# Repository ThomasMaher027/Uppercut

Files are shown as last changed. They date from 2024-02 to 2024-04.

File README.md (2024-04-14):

# Projet S4GRO 2024 - Uppercut
Le Uppercut est un projet ayant pour but de concevoir un bras robotique de type *Shadow boxer*, inspiré du film [*Real Steel*](https://youtu.be/wD0goULgueE?si=wrtzg6bM562aRAEw).
Le projet s'est divisé en 3 objectifs : concevoir un bras robotique à 4 axes, atteindre des positions cibles avec précision et utiliser une caméra pour contrôler le robot. 

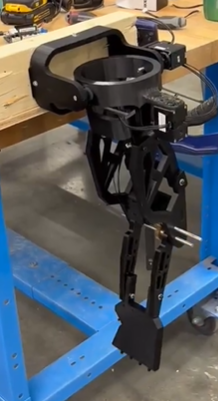
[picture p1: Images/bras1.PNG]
image du bras robotique


##  Guide du répertoire
Voici un guide de l'organisation des dossiers :
- Le dossier [*Arduino*](https://github.com/ThomasMaher027/Uppercut/tree/main/Arduino) contient le code utilisé sur la carte Arduino pour contrôler les moteurs.
- Le dossier [*Informatique*](https://github.com/ThomasMaher027/Uppercut/tree/main/Informatique) contient le code Python pour analyser l'information de la caméra.
- Le dossier [*Mécanique*](https://github.com/ThomasMaher027/Uppercut/tree/main/Mécanique) contient l'analyse dynamique du système et des CAD du robot.

## Procédure de lancement
Voici la procédure de fonctionnement du robot une fois qu'il est assemblé.
1. Télécharger les fichiers de code pour la caméra se trouvant dans le dossier [main/Informatique/Projet_s4/code_final_utiliser](https://github.com/ThomasMaher027/Uppercut/tree/main/Informatique/Projet_s4/code_final_utiliser)
2. Télécharger les fichiers de code pour contrôler les moteurs dans le dossier [main/Arduino/ArduinoIDE/controle_moteur](https://github.com/ThomasMaher027/Uppercut/tree/main/Arduino/ArduinoIDE/controle_moteur)
3. Suivre le [guide pour l'utilisation de la carte OpenRB-150](https://youtu.be/RaNzGhQzlu4?si=twsLND9ONWHosGwk)
4. Téléverser le code [controle_moteur.ino](https://github.com/ThomasMaher027/Uppercut/blob/main/Arduino/ArduinoIDE/controle_moteur/controle_moteur.ino) dans la carte OpenRB-150 à partir de [l'IDE d'Arduino](https://www.arduino.cc/en/software)
5. Laisser l'ordinateur connecté à la carte OpenRB avec le câble USB et ne pas ouvrir le moniteur série dans l'IDE d'Arduino.
6. Lancer le code [Holistic_TempsReel_Angle_communicationSerie.py](https://github.com/ThomasMaher027/Uppercut/blob/main/Informatique/Projet_s4/code_final_utiliser/Holistic_TempsReel_Angle_communicationSerie.py) dans un IDE Python (par exemple : [PyCharm](https://www.jetbrains.com/pycharm/)) sur un ordinateur branché à une caméra
7. Pour arrêter le programme, appuyer sur la touche "q" quand la fenêtre de la caméra est ouverte
8. S'assurer d'appuyer sur le bouton "*reset*" de la carte OpenRB avant de relancer le code Python

## Vidéos de présentation
Voici une vidéo du robot contrôlé en temps réel

https://github.com/ThomasMaher027/Uppercut/assets/114596560/83d8d1ad-10cf-46f6-bbb1-c36d5d543623

Et ici, une vidéo du robot qui éxécute une séquence prédéfini de mouvement

https://github.com/ThomasMaher027/Uppercut/assets/114596560/a4b2e40c-ad0c-4941-9826-d2be24af7056

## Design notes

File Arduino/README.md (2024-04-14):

# Uppercut
Voici le code pour une carte [OpenRB-150 de Robotis](https://emanual.robotis.com/docs/en/parts/controller/openrb-150/) pour contrôler les moteurs Dynamixels. L'ensemble est configuré pour être utilisé avec l'IDE d'Arduino.

Le code principale est situé dans [Arduino/control_moteur.ino](https://github.com/ThomasMaher027/Uppercut/blob/main/Arduino/ArduinoIDE/controle_moteur/controle_moteur.ino).

Il y a 2 modes de fonctionnement : temps réel et choix de mouvement. Pour choisir le mode, commenter/décommenter la fonction loop() appropriée.

Le dossier [PlatformIO](https://github.com/ThomasMaher027/Uppercut/tree/main/Arduino/PlaformIO) contient les fichiers pour faire fonctionner le code grâce à PlatformIO. Cependant, nous avons rencontré des problèmes avec PlatformIO et avons préféré d'utiliser l'IDE d'Arduino (mais rien n'empêche d'essayer de l'utiliser).

## Personnalisation
Certaines variables du programme qui peuvent/doivent être modifiées selon le contexte d'utilisation. En voici la liste :
- nb_moteur (controle_moteur.ino, mouv_prenregistres.cpp et real_time.cpp)
- DXL_ID : identidiant des moteurs Dynamixel. Faire attention à l'ordre dans lequel les moteurs sont initiés (controle_moteur.ino, mouv_prenregistres.cpp et real_time.cpp)
- vit_max (real_time.cpp)
- vit_min (real_time.cpp)
- nb_mouvement : indique le nombre de mouvements préenregistrés totaux (mouv_prenregistres.cpp)
- combinaison : combinaison de mouvement à faire (controle_moteur.ino)

## Temps réel
Le temps utilise le serialCommunication.h pour lire le port série et extraire l'information de message. Le message reçu par l'Arduino est une chaine de caractère de la forme suivante : "<cible1,cible2,cible3,cible4>. Les cibles sont extraite et enregistrer dans le tableau _mgs_donnees_.

## Choix mouvement
Pour le choix de mouvement, l'Arduino lit le port série pour 1 chiffre. Ensuite, fait correspondre le chiffre lu à un mouvement préenregistré.

### Pour ajouter des mouvements
La structure _structStance_ contient les informations de chaque mouvement. Il contient : 
- Un identifiant
- Un nombre de sous-mouvement
- Un tableau de cibles

Pour ajouter un mouvement indiquer le nombre de sous-mouvement on souhaite diviser le mouvement complet. Ensuite, le tableau de cibles fonction de la façon suivante : pour n moteur, les n premières valeurs correspondent aux cibles du 1er sous-mouvement. Les n prochaines correspondent aux prochaines cibles du 2e sous-mouvement. Le tableau de cible a une taille de k*n, k étant le nombre de sous-mouvement. Les cibles sont ordonnés selon l'ordre dans lequel les identifiants des moteurs a été défini.

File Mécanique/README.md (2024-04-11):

# ASSEMBLAGE MÉCANIQUE
Toutes les impressions sont faites à 15% infill en fast (0,2mm).
## ASSEMBLAGE DE L'ÉPAULE

Il faut d'abord imprimer les éléments suivant :
- **1x** [0001.SLDPRT](https://github.com/ThomasMaher027/Uppercut/tree/main/Mécanique/3D%20CAD/En%20cours/Épaule_test_2)
- **1x** [0002.SLDPRT](https://github.com/ThomasMaher027/Uppercut/tree/main/Mécanique/3D%20CAD/En%20cours/Épaule_test_2)
- **1x** [0003.SLDPRT](https://github.com/ThomasMaher027/Uppercut/tree/main/Mécanique/3D%20CAD/En%20cours/Épaule_test_2)
- **2x** [Adapteur_boost.SLDPRT](https://github.com/ThomasMaher027/Uppercut/tree/main/Mécanique/3D%20CAD/En%20cours/Coude_VF)
    - À imprimer avec plus de précison, par exemple : Fine, 80% infill.

Il faut ensuite se procurer les éléments suivant :
- **2x** [Shaft 1/4 de longueur 180mm et 135mm](https://ca.robotshop.com/products/actobotics-12x1-4-precision-d-shaft)
- **2x** [moteur dynamixel XM430-W350-T](https://emanual.robotis.com/docs/en/dxl/x/xm430-w350/)
	
Pour faire l'assemblage, il faut fixer 0001 et 0002 à l'aide d'un shaft. Ensuite, il faut visser l'adaptateur à un moteur et positionner celui-ci du côté de son support. Il ne reste qu'à visser le moteur à sa base. 

Il faut ensuite refaire ces manipulations pour la pièce 0002 et 0003. Vous pouvez vous fier à la figure 1 pour visualiser le modèle correctement.Il faut faire attention à la bonne orientation des pièces. 

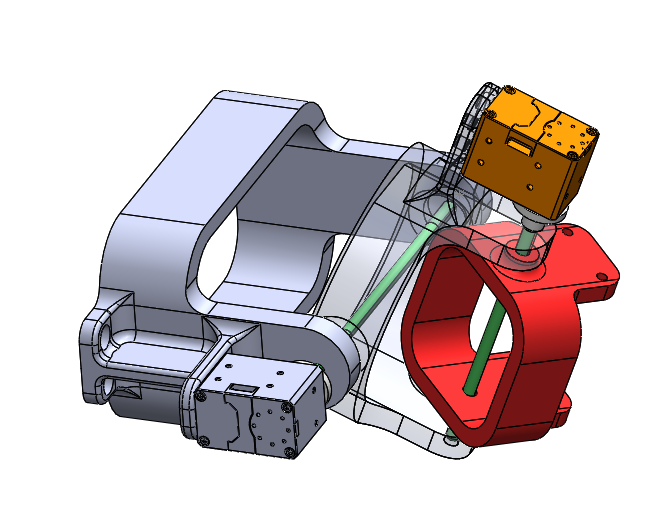
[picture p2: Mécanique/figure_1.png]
Figure 1 : Modèle 3D de l'épaule


*Figure 1 : Modèle 3D de l'épaule*

## ASSEMBLAGE DU BICEP
Il faut d'abord imprimer les éléments suivant :
- **2x** [Bicep_base.SLDPRT](https://github.com/ThomasMaher027/Uppercut/tree/main/Mécanique/3D%20CAD/En%20cours/Coude_VF)
- **1x** [Fixation_moteur.SLDPRT](https://github.com/ThomasMaher027/Uppercut/tree/main/Mécanique/3D%20CAD/En%20cours/Coude_VF)
- **1x** [Fixation_bicep.SLDPRT](https://github.com/ThomasMaher027/Uppercut/tree/main/Mécanique/3D%20CAD/En%20cours/Coude_VF)
- **1x** [Adaptateur.SLDPRT](https://github.com/ThomasMaher027/Uppercut/tree/main/Mécanique/3D%20CAD/En%20cours/Coude_VF)
    - À imprimer avec plus de précison, par exemple : Fine, 80% infill.

Il faut ensuite se procurer les éléments suivant :
- **2x** [Shaft 1/4 de longueur 100mm et 50mm](https://ca.robotshop.com/products/actobotics-12x1-4-precision-d-shaft)
- **1x** [moteur dynamixel XL430-W250-T](https://emanual.robotis.com/docs/en/dxl/x/xl430-w250/)
- **2x** [32T, 0.250" (1/4) Bore 32P Shaft Mount Pinion Gear](https://www.servocity.com/32t-0-250-1-4-bore-32p-shaft-mount-pinion-gear/)

Pour faire l'assemblage, il faut d'abord fixer les deux Bicep_base et Fixation_moteur à l'aide de la quincaillerie. Ensuite, il faut insérer la Fixation du moteur de la même orientation que la figure 2.
	
Il faut visser l'adaptateur sur le moteur et insérer un premier shaft au bout de Bicep_base. Avant de l'insérer au complet, il faut ajouter dans l'ordre une partie de l'avant-bras, un engrenage 16T et l'autre partie de l'avant-bras.
	
Enfin, il faut insérer le deuxième shaft comme sur la figure 2, y ajouter l'engrenage 32T et positionner le moteur vis-à-vis les 4 trous de sa fixation. Il ne reste qu'à bien fixer le moteur et aligner les deux engrenages, en s'étant assuré de ne pas oublier de brancher les fils au moteur avant de le fixer.  

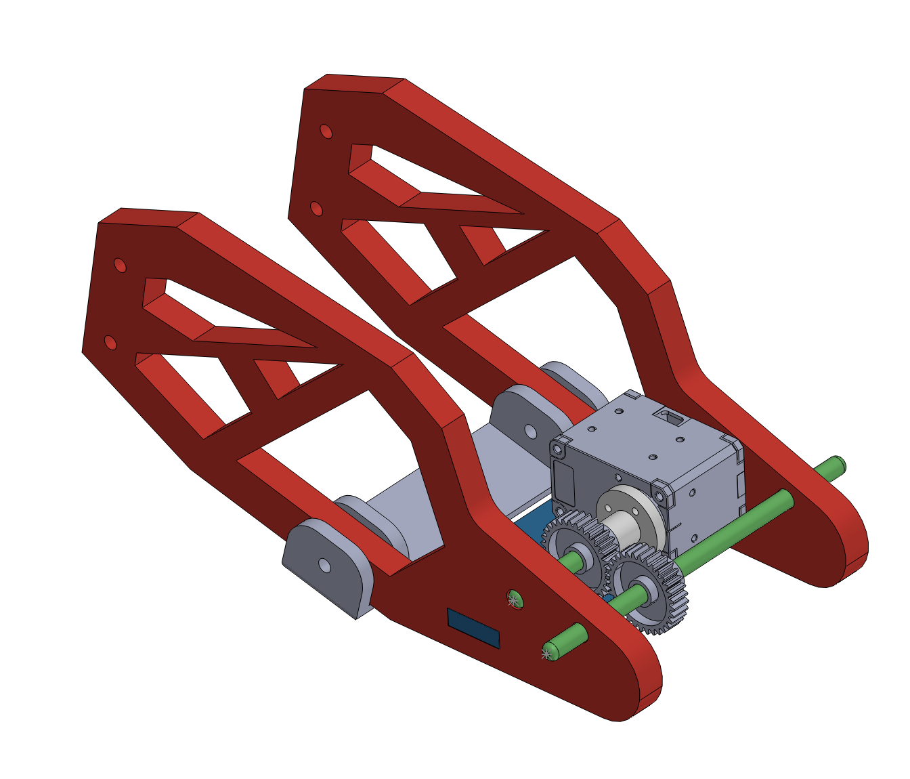
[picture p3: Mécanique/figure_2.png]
Figure 2 : Modèle 3D du biceps


*Figure 2 : Modèle 3D du biceps*

## ASSEMBLAGE DE L'AVANT-BRAS
Pour faire l'avant-bras, il faut simplement fixer le rouleau_doigts au moteur et fixer le moteur à son support. Ensuite il faut assembler les 2 pièces d'Avant_Bras sur les côtés et les fixer au biceps avec le shaft ainsi qu'à la main à l'autre extrémité.
	
Il faut d'abord imprimer les éléments suivant :
- **2x** [Avant_Bras.SLDPRT](https://github.com/ThomasMaher027/Uppercut/tree/main/Mécanique/3D%20CAD/En%20cours/Avant_Bras)
- **1x** [Support_Avant_Bras_moteur.SLDPRT](https://github.com/ThomasMaher027/Uppercut/tree/main/Mécanique/3D%20CAD/En%20cours/Support)
- **1x** [Support_files_main.SLDPRT](https://github.com/ThomasMaher027/Uppercut/tree/main/Mécanique/3D%20CAD/En%20cours/Avant_Bras)
- **1x** [Poulie_1.SLDPRT](https://github.com/ThomasMaher027/Uppercut/tree/main/Mécanique/3D%20CAD/En%20cours/Avant_Bras)
- **1x** [Poulie_2.SLDPRT](https://github.com/ThomasMaher027/Uppercut/tree/main/Mécanique/3D%20CAD/En%20cours/Avant_Bras)

Il faut ensuite se procurer l'élément suivant :
- **1x** [moteur dynamixel XL430-W250-T](https://emanual.robotis.com/docs/en/dxl/x/xl430-w250/)

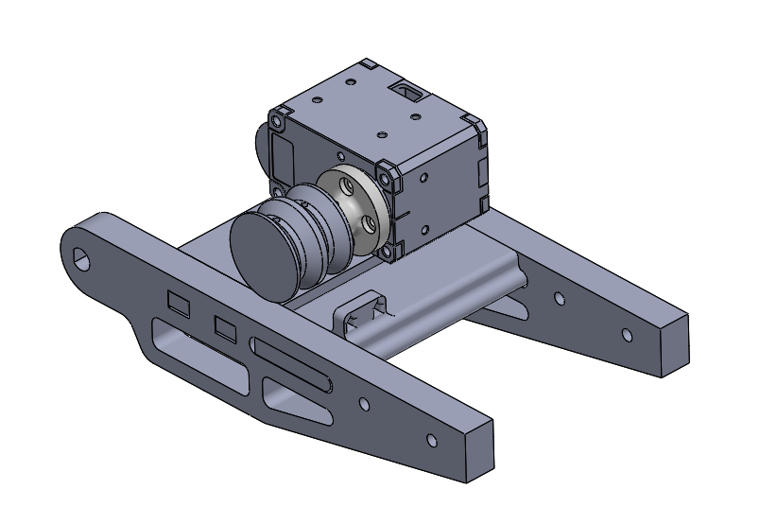
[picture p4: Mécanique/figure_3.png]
Figure 3 : Modèle 3D de l'avant-bras


*Figure 3 : Modèle 3D de l'avant-bras*

## ASSEMBLAGE DE LA MAINMAIN
Il faut d'abord imprimer les éléments suivant :
- **9x** [Doigt1.SLDPRT](https://github.com/ThomasMaher027/Uppercut/tree/main/Mécanique/3D%20CAD/En%20cours/doigt)
    - À imprimer avec plus de précison, par exemple : Fine (0.1mm), 20% infill.
- **5x** [Doigt2.SLDPRT](https://github.com/ThomasMaher027/Uppercut/tree/main/Mécanique/3D%20CAD/En%20cours/doigt)
    - À imprimer avec plus de précison, par exemple : Fine (0.1mm), 20% infill.
- **1x** [paume_V3.SLDPRT](https://github.com/ThomasMaher027/Uppercut/tree/main/Mécanique/3D%20CAD/En%20cours/Paume)

Il faut ensuite se procurer l'élément suivant :
- **1x** Environ 30 cm de PLA 2,85mm de diamètre pour assembler les doigts
	
Pour assembler la main il faut faire 4 doigts et 1 pouce. Les doigt sont fait en connectant 2 Doigt1 et 1 Doigt2. Le pouce est fait en connectant 1 Doigt1 et 1 Doigt2. Pour faire la connexion il faut passer un bout de filament PLA dans les connecteurs rond puis faire fondre les bouts pour le garder en place.
	
Après, il faut passer le fil de pêche dans les doigts et l'attacher au bout du doigt. Il peut aussi être intéressant d'utiliser de la colle.
	
Ensuite il faut connecter les doigts à la paume de la même façon que les segments de doigt se connectent ensemble.

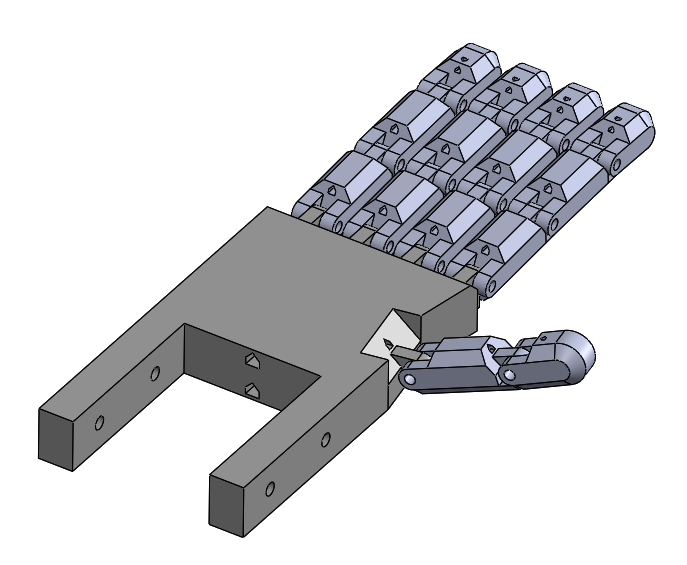
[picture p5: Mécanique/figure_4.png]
Figure 4 : Modèle 3D de la main


*Figure 4 : Modèle 3D de la main*

## ASSEMBLAGE COMPLET
	
Il faut fixer le biceps à l'épaule à l'aide de 4 vis M4 25LG, 4 écrous et 4 rondelles. Il faut ensuite fixer le bras à sa base à l'aide de 4 vis M6 50LG, 4 écrous et 4 rondelles et de même pour la main, en s'assurant que les fils de pêche puisse bien s'enrouler autour de la poulie de l'avant-bras et passer dans les trous correspondant. Il faut les enrouler de manière opposé afin qu'il ouvre et/ou ferme la main.

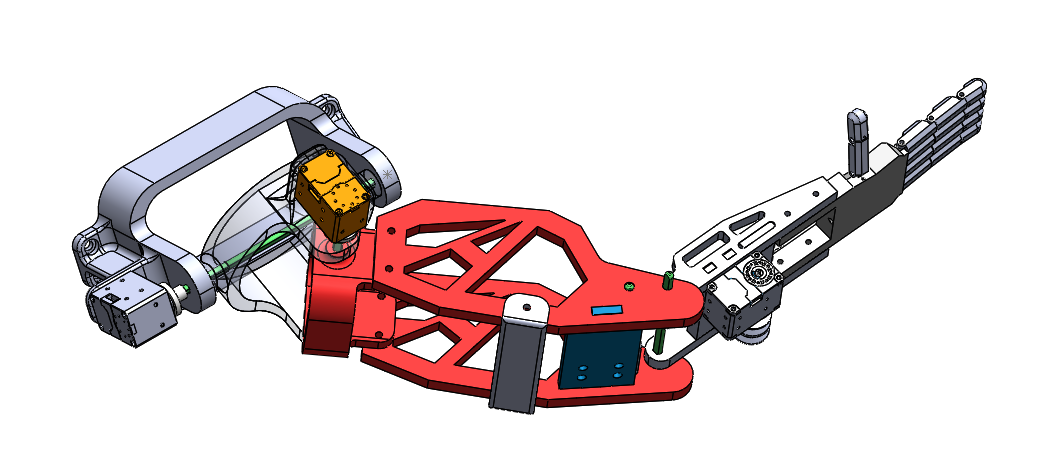
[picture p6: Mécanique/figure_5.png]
Figure 5 : Modèle 3D du bras entier


*Figure 5 : Modèle 3D du bras entier*

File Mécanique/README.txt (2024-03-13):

ASSEMBLAGE MÉCANIQUE

ASSEMBLAGE DE L'ÉPAULE
	Il faut d'abord imprimer les éléments suivant :
	- 1x 0001.SLDPRT
	- 1x 0002.SLDPRT
	- 1x 0003.SLDPRT
	Il faut ensuite se procurer les éléments suivant :
	- 2x shaft 1/4 de longueur 180mm et 135mm
	- 2x moteur dynamixel XM,H-430
	- 2x Adapteur_boost du moteur au shaft
	
	Pour faire l'assemblage, il faut fixer 0001 et 0002 à l'aide d'un shaft. Ensuite, il faut visser l'adaptateur à un moteur et positionner celui-ci du côté de son support. Il ne reste qu'à visser le moteur à sa base. 

	Il faut ensuite refaire ces manipulations pour la pièce 0002 et 0003. Vous pouvez vous fier à la figure 1 pour visualiser le modèle correctement.Il faut faire attention à la bonne orientation des pièces. 

ASSEMBLAGE DU BICEP
	Il faut d'abord imprimer les éléments suivant :
	- 2x Bicep_base.SLDPRT
	- 1x Fixation_moteur.SLDPRT
	- 1x Fixation_bicep.SLDPRT
	- 1x Adaptateur.SLDPRT
	Il faut ensuite se procurer les éléments suivant :
	- 2x shaft de longueur 100mm et 50mm
	- 1x moteur dynamixel XL,H-430
	- 1x Gear 32T
	- 1x Gear 16T

	Pour faire l'assemblage, il faut d'abord fixer les deux Bicep_base et Fixation_moteur à l'aide de la quincaillerie. Ensuite, il faut insérer la Fixation du moteur de la même orientation que la figure 2.
	
	Il faut visser l'adaptateur sur le moteur et insérer un premier shaft au bout de Bicep_base. Avant de l'insérer au complet, il faut ajouter dans l'ordre une partie de l'avant-bras, un engrenage 16T et l'autre partie de l'avant-bras.
	
	Enfin, il faut insérer le deuxième shaft comme sur la figure 2, y ajouter l'engrenage 32T et positionner le moteur vis-à-vis les 4 trous de sa fixation. Il ne reste qu'à bien fixer le moteur et aligner les deux engrenages, en s'étant assuré de ne pas oublier de brancher les fils au moteur avant de le fixer.  

ASSEMBLAGE DE L'AVANT-BRAS
	Pour faire l'avant-bras, il faut simplement fixer le rouleau_doigts au moteur et fixer le moteur à son support. Ensuite il faut assembler les 2 pièces d'Avant_Bras sur les côtés et les fixer au biceps avec le shaft ainsi qu'à la main à l'autre extrémité.
	
	Liste de pièces:
	- 2x Avant_Bras.SLDPRT
	- 1x Support_Avant_Bras_moteur.SLDPRT
	- 1x moteur dynamixel XL,H-430
	- 1x rouleau_doigts

ASSEMBLAGE DE LA MAIN:
	Pour faire la main il faut avoir:
	- 9 exemplaires de Doigt1
	- 5 exemplaires de Doigt2
	- 1 exemplaire de paume_V3
	- 1 bobine de PLA 2,75mm de large
	
	Pour assembler la main il faut faire 4 doigts et 1 pouce. Les doigt sont fait en connectant 2 Doigt1 et 1 Doigt2. Le pouce est fait en connectant 1 Doigt1 et 1 Doigt2. Pour faire la connexion il faut passer un bout de filament PLA dans les connecteurs rond puis faire fondre les bouts pour le garder en place.
	
	Après, il faut passer le fil de pêche dans les doigts et l'attacher au bout du doigt. Il peut aussi être intéressant d'utiliser de la colle.
	
	Ensuite il faut connecter les doigts à la paume de la même façon que les segments de doigt se connectent ensemble.

ASSEMBLAGE COMPLET
	
	Bicep et épaule : Il faut fixer le biceps à l'épaule à l'aide de 4 vis M4 25LG, 4 écrous et 4 rondelles.
	
	Il faut ensuite fixer le bras à sa base à l'aide de 4 vis M6 50LG, 4 écrous et 4 rondelles.

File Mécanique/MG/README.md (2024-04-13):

# Dossier
Dans ce dossier les fichiers servent à vérifier les comportements de notre système avec motionGenesis.

# Fichier
le DCL suivant représente notre système de manière simple.

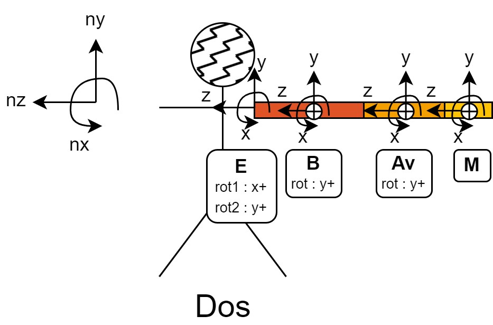
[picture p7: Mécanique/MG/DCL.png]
image du DCL


L'épaule à été défini en un rigidFrame (E) pour la rotation nx et un rigidBody (B) pour la rotation ey. 
le rigidbody Av sert à repérésenter la rotation du coude et le rigidbody M représente la main.
Les particules MotE, MotC et MotM servent à représenter le moteur pour la 2e rotation de l'épaule, le moteur pour le coude et le moteur pour ouvrir et fermer les doigts de la main.

Les constantes mMotp et mMotg servent à définir la masse des particules moteurs.
mMotp est pour les XL430. 
mMotg est pour les XM430.

Les constantes Lb, LAv et LM représentent la longueur du bicep, la longueur de l'avant bras et la longueur de la main.
Les constantes avec cmx, cmy et cmz sevent à positionner le centre de masse des différents corps.
Les constantes dMotM et dMotE servent à positionner le moteur pour la 2e rotation de l'épaule et le moteur pour les doigts de la main.

## StatiqueBras.txt
Les variables Te, Tb et Tc sont inconnues et elles servent à savoir quels couples les moteurs pour l'épaule et le coude doivent développer pour garder une position statique déterminer avec les angles qe, qb et qc.

notre analyse se fait dans 2 positions pour l'instant :
```
%Constant qe = 0 deg, qb = 0 deg, qc = 0 deg %bras droit a coter (demi Tpose)
Constant qe = -90 deg, qb = 90 deg, qc = 0 deg %lever devant (pointer)
```
Dans les deux position, le bras est à l'horizontale et compètement droit. La 1ere, le bras est parallèle à la poitrine. Dans la 2e, le bras est perpendiculaire à la poitrine.

## DynamiqueBras.txt
Pour faire une bonne analyse dynamique, il faut ajouter les inerties des membres. Elles ont été calculés avec solidwork et les assemblages dans la section 3D CAD.

Dans cette analyse, le coude est toujours déplier (qc = 0 deg). L'anaylse est faite sur un tour, 360 deg. 
Si c'est le 1er moteur qui travail à 2.95 Nm on regarde son acceleration (qe'') et les couples au coude et à l'autre moteur de l'épaule. Le bras est complètement droit, qb est à 0 deg. 
Si c'est le 2e moteur qui travail à 2.95 Nm on regarde son acceleration (qb'') et les couples au coude et au 1er moteur de l'épaule. Le bras est complètement droit, qe est à -90 deg

Selon le moteur regarder, on commence dans la position statique y faisant référence. 
moteur 1 = 1ere position statique au départ. le tour se fait autour de nx.
moteur 2 = 2e position statique au départ. le tour se fait autour de ey et ressemble à un lancer de balle donnée.

```
B.SetInertia(Bcm, IBxx = 0.00136096 kg*m^2, IByy = 0.00105899 kg*m^2, IBzz = 0.00064248 kg*m^2,  IBxy = -0.00000034 kg*m^2, IByz =  -0.00001995 kg*m^2, IBzx = -0.00012044 kg*m^2)
Av.SetInertia(Avcm, IAvxx = 0.00018089 kg*m^2, IAvyy = 0.00011084 kg*m^2, IAvzz = 0.00007775 kg*m^2,  IAvxy = 0 kg*m^2, IAvyz =  0 kg*m^2, IAvzx = 0.00000058 kg*m^2)
M.SetInertia(Mcm, IMxx = 0.00016081 kg*m^2, IMyy = 0.00012716 kg*m^2, IMzz = 0.00003633 kg*m^2,  IMxy = 0.00000009 kg*m^2, IMyz =  -0.00000214 kg*m^2, IMzx = -0.00000098 kg*m^2)
```

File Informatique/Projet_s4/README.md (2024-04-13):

# Système de Vision 

## Début et recherche utile pour comprendre le cheminement du côté de la vision
le fichier suivant présente comment mettre en place l'environnement de programmation et quelles vidéos ont aider le choix des librairies et le choix du language de programmation utilisé :
[doc_vision](https://github.com/ThomasMaher027/Uppercut/blob/main/Informatique/Projet_s4/Projet_S4_recherche_Camera_Python.docx)

## Temps Réel
À l'aide des librairies OpenCv et MediaPipe, le flux vidéo de la caméra est analyser et des angles sont calculés. 
Les angles calculés sont ceux du coude et de l'épaule. Pour l'épaule, il y a deux angles de calculés. Le 1er est celui fait entre le vecteur (épaule droite à épaule gauche) et le vecteur (épaule droite à coude droit). Le 2e est celui fait entre le vecteur (épaule droite à hanche droite) et le vecteur (épaule droite à coude droit). Il y a aussi une analyse de fait pour savoir si la main est fermé ou non. Les 3 angles filtrés et le resultats de l'analyse de la main sont envoyés à l'openRB par port série.

## Mouvements prédéfinis
Le programme de vision permet d'analyser des mouvements prédéfinie du bras gauche d'un utilisateur pour envoyer les mouvements lus à un arduino par communication port série. 
Les 4 mouvements sont:
- flexion du coude
- abduction/adduction du bras parallèle au corps
- abduction/adduction du bras perpendiculaire au corps
- Léver du bras au-dessus de l'épaule ( position pour poser une question)
Pour des informations supplémentaires sur les fonctions du programme, consulter [MediaPipe](https://developers.google.com/mediapipe) sur internet.

## Classe de filtrage
La classe dataAngle située dans [filteDonnees](https://github.com/ThomasMaher027/Uppercut/blob/main/Informatique/Projet_s4/filtreDonnees.py).
Cette classe enregistre les valeurs d'angle calculées par la caméra et applique un filtre sur les données.

3 filtres sont disponibles : 
- Une moyenne mobile
- Un filtre RIf passe-bas
- Un filtre RII passe-bas (Butterworth)

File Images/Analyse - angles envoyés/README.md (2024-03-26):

# Comparaison entre les angles calculés à partir de la caméra avec les angles filtrés par une moyenne mobile
Le début et la fin de chaque graph ne sont pas tout à fait représentatif, à cause qu'il faut bouger pour partir et arrêter le programme.
## Cas #1 : bras immobile 
### Mouvement épaule : avant-arrière
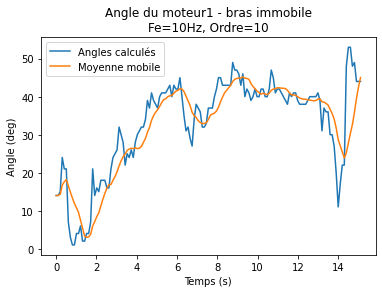
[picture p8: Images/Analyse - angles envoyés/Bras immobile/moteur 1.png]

### Mouvement épaule : côté
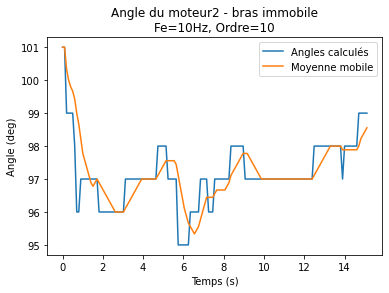
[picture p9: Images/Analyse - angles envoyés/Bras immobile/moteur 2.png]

### Mouvement coude
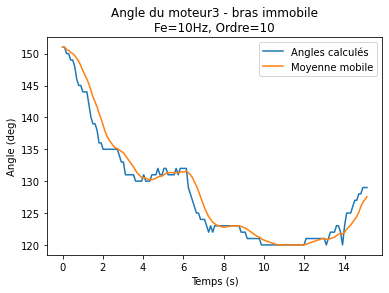
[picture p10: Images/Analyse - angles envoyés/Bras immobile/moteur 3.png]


## Cas #2 : contraction du biceps
### Mouvement épaule : avant-arrière
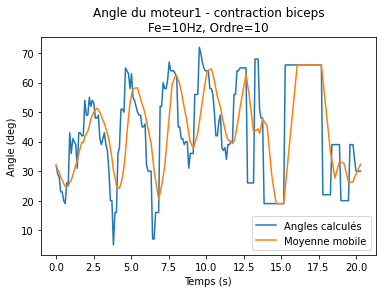
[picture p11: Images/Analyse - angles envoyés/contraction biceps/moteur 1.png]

### Mouvement épaule : côté
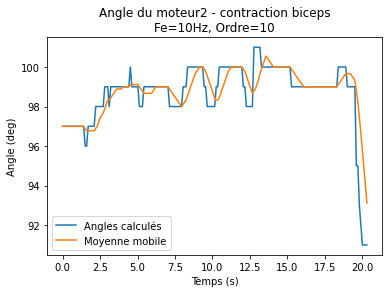
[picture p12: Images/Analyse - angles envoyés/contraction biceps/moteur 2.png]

### Mouvement coude
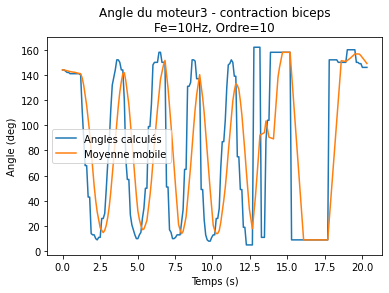
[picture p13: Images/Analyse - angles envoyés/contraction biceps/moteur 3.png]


J'ai fait plusieurs répétitions lentes (? le nombre), 5 répétitions à vitesse moyenne et 5 rapides. La fréquence d'échantillonnage n'est pas assez grande pour lire avec précision des mouvement de moyenne à haute intensités.

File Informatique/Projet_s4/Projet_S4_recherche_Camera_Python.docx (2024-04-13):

Notes recherche détection mouvement avec python et caméra :

Bigger picture:

https://www.kdnuggets.com/2022/08/perform-motion-detection-python.html

Example of code and explanation: simple

https://medium.com/@gowtham180502/motion-detection-and-tracking-using-opencv-python-ea75ef927e72

https://pyimagesearch.com/2015/05/25/basic-motion-detection-and-tracking-with-python-and-opencv/

youtube to see what can be done: simple

https://www.youtube.com/watch?v=731tP7t1BOc

other detection : usable

https://www.youtube.com/watch?v=gsktsIc4Fjs

these will be good ref:

https://www.youtube.com/watch?v=pG4sUNDOZFg

https://www.youtube.com/watch?v=9iEPzbG-xLE&list=PLMoSUbG1Q_r8jFS04rot-3NzidnV54Z2q

https://www.youtube.com/watch?v=7wsY6Roehe0

https://www.youtube.com/watch?v=7KV5489rL3chttps://www.youtube.com/watch?v=7KV5489rL3c

other cool :

https://www.youtube.com/watch?v=JPCIg0IIgpQ

https://www.youtube.com/watch?v=J2bv6BGSIXk&list=PLBg7GSvtrU2OaYp2F-FqqZk0RUB4IUvvb

https://www.youtube.com/watch?v=_cueQFM_AzY

https://www.youtube.com/watch?v=h8Di-NDkCGs

How to download stuff for pycharm :

First setup new project

Then go in settings

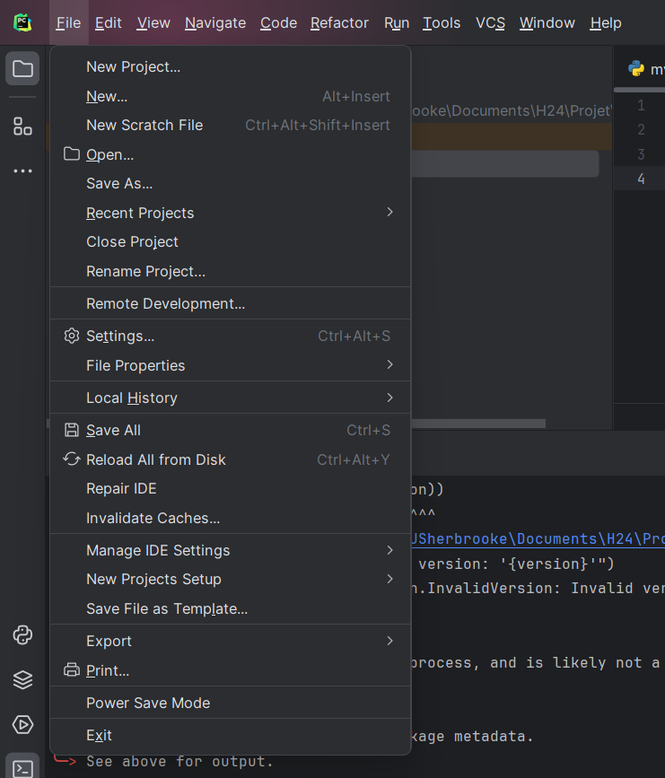
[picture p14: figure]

Then python interpreter:

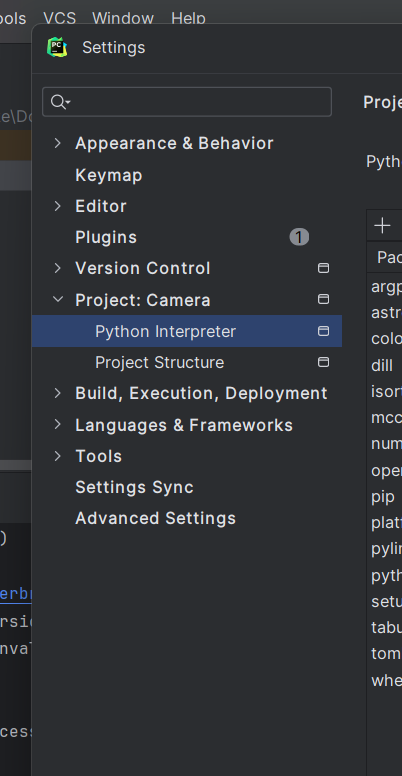
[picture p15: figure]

Then add

You will need these:

Then you go in terminal

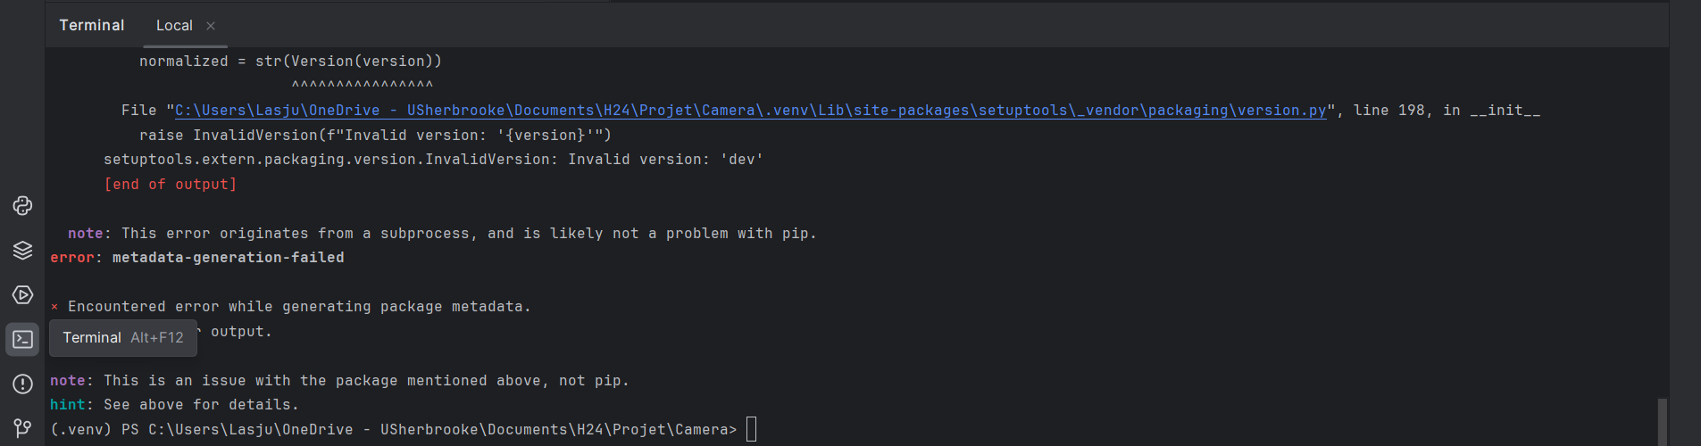
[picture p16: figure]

And write lines :

pip install opencv-python

And

Pip install mediapipe (python 3.8-3.11 not 3.12)

To choose python 3.11 it must be installed before creating project

Super Super interesting (this dude is doing our project)

AI Pose Estimation with Python and MediaPipe | Plus AI Gym Tracker Project (youtube.com) (https://www.youtube.com/watch?v=06TE_U21FK4)

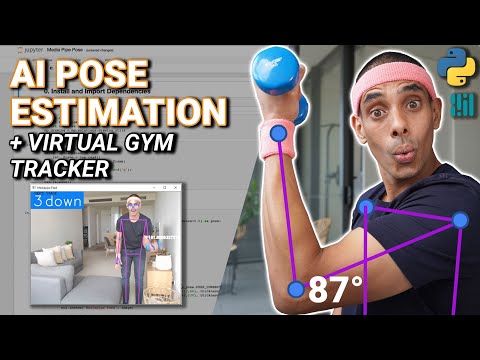
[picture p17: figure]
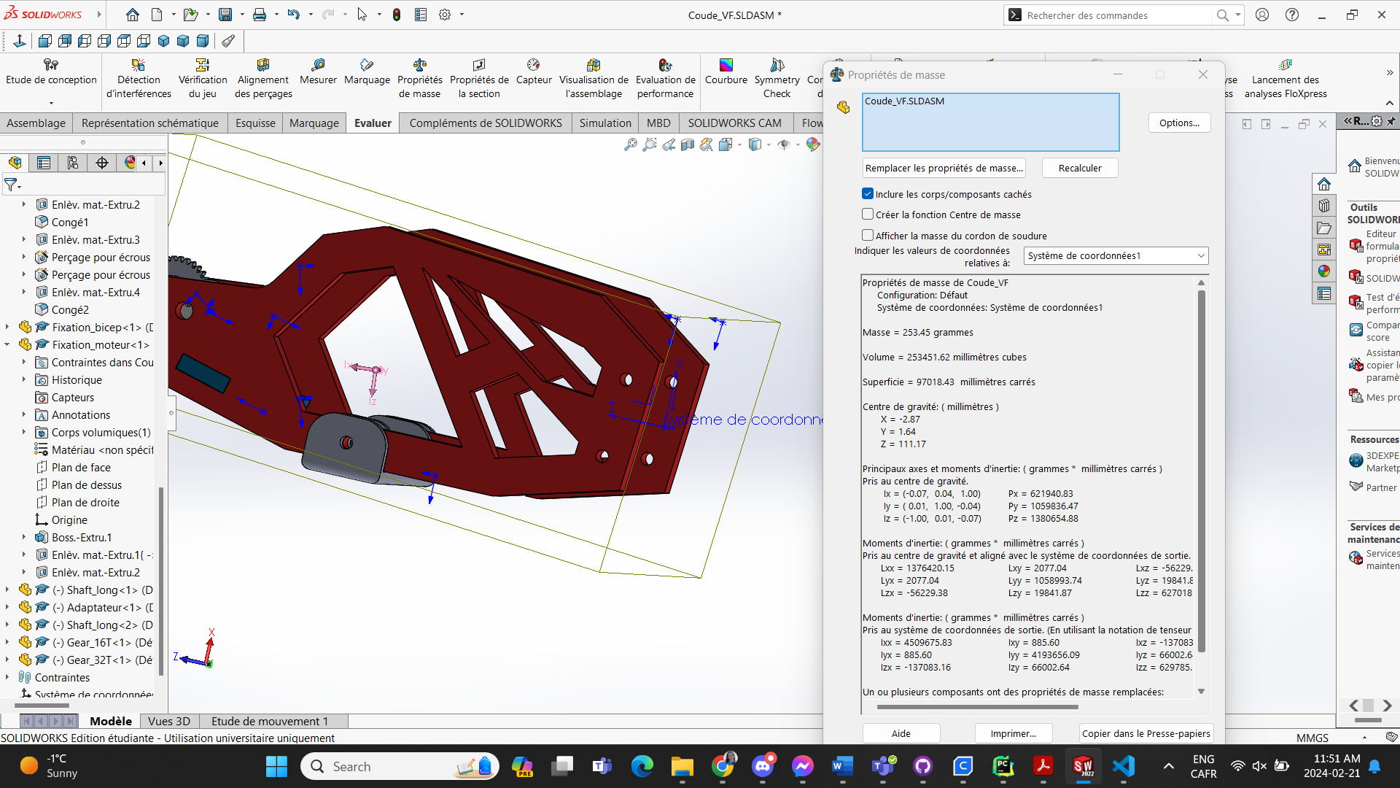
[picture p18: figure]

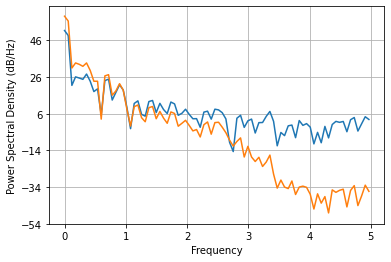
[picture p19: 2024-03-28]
Images/Analyse - angles envoyés/FIRvsIIR/Figure 2024-03-28 094442 (4).png

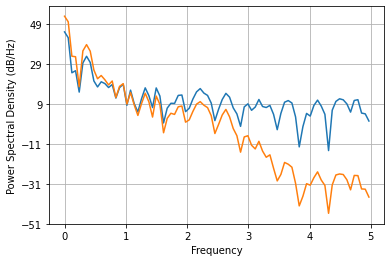
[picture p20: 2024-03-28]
Images/Analyse - angles envoyés/FIRvsIIR/Figure 2024-03-28 094442 (3).png

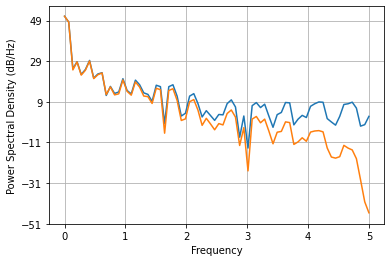
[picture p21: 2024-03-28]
Images/Analyse - angles envoyés/FIRvsIIR/Figure 2024-03-28 094442 (10).png

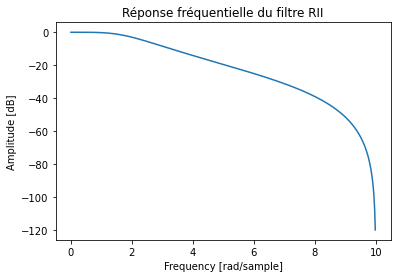
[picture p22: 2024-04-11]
Images/Analyse - angles envoyés/Graph - Livraison 2/Reponse fréq RII.png

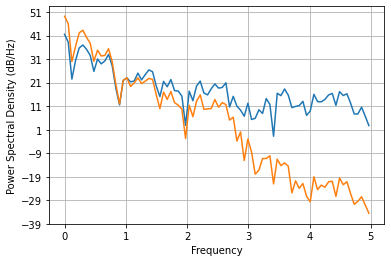
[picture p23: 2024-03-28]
Images/Analyse - angles envoyés/FIRvsIIR/Figure 2024-03-28 094442 (5).png

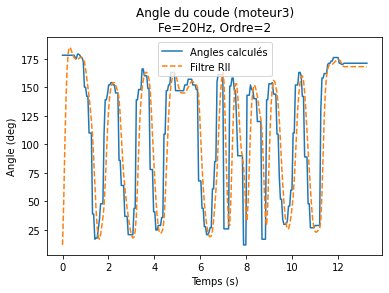
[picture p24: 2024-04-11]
Images/Analyse - angles envoyés/Graph - Livraison 2/Angles filtrés RII.png

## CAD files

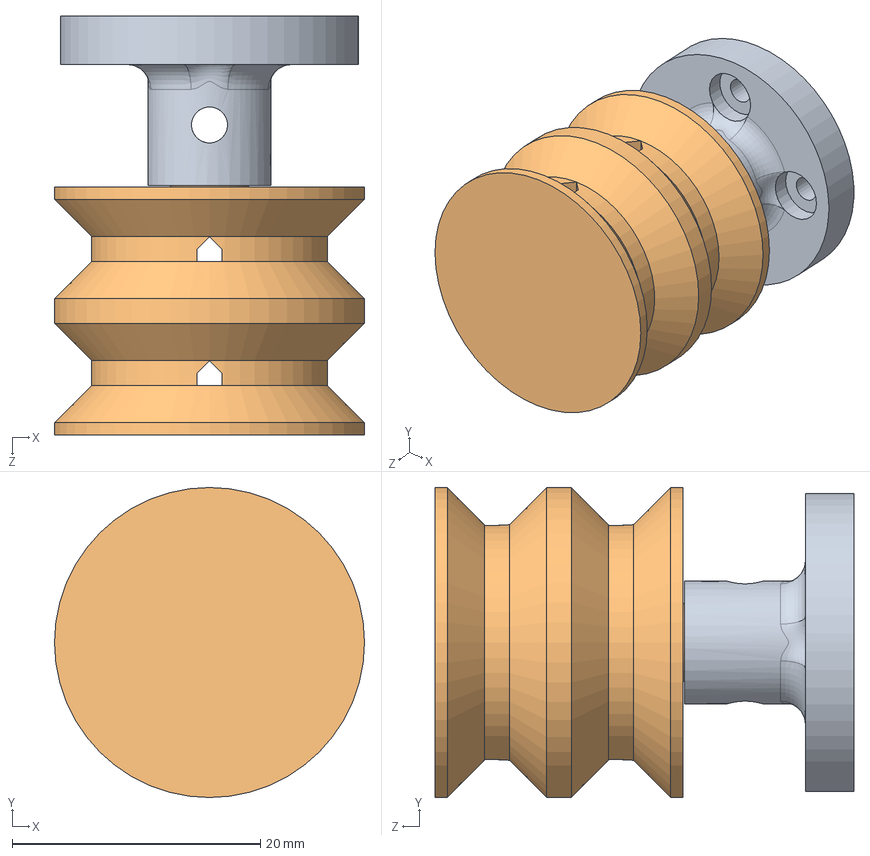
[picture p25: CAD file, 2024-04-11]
Mécanique/3D CAD/En cours/Avant_Bras/Poulie.SLDASM
25.0 x 25.0 x 33.8 mm
Poulie
Poulie_2

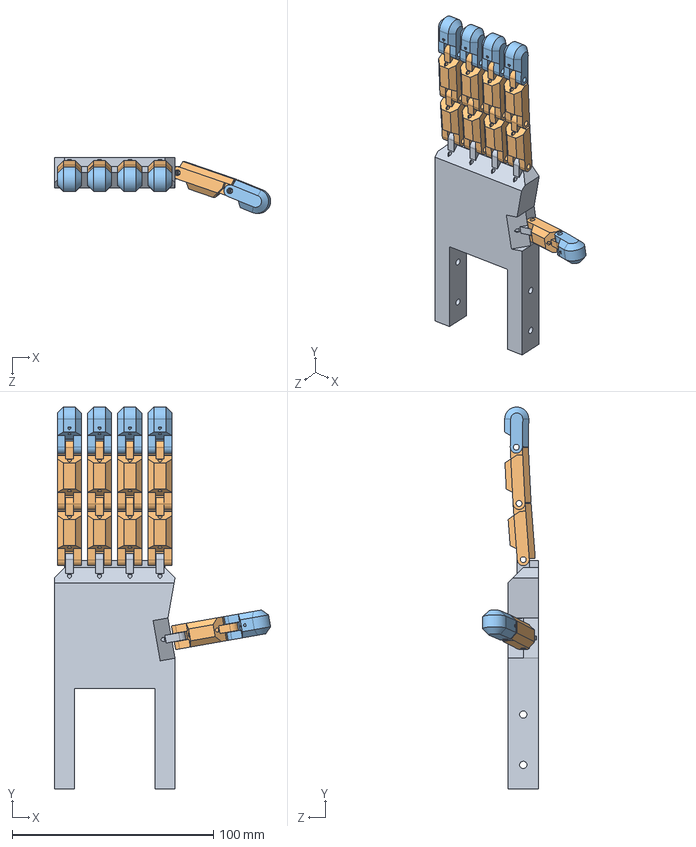
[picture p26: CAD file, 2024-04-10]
Mécanique/3D CAD/En cours/Paume/main.SLDASM
107.5 x 189.9 x 27.7 mm
Paume_V4
Doigt_test_1 x 9
Doigt_test_2 x 5

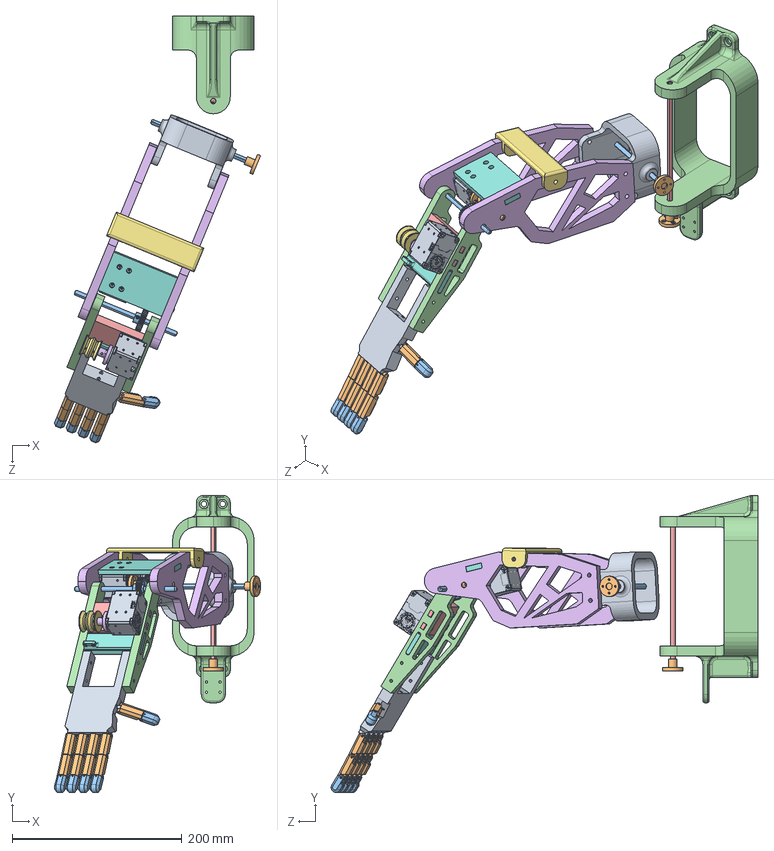
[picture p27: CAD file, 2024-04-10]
Mécanique/3D CAD/En cours/VF_ROBOT_ARM/Assemblage1.SLDASM
242.8 x 349.6 x 502.3 mm
Adaptateur x 3
Shaft_long_court x 2
Shaft_long
Bicep_base x 2
Fixation_bicep
Fixation_moteur
Petit_moteur x 2
Shaft
Gear_32T x 2
Avant_Bras x 2
Support_Avant_Bras_Moteur
Poulie
Poulie_2
Support_files_main
Paume_V4
Doigt_test_1 x 9
Doigt_test_2 x 5

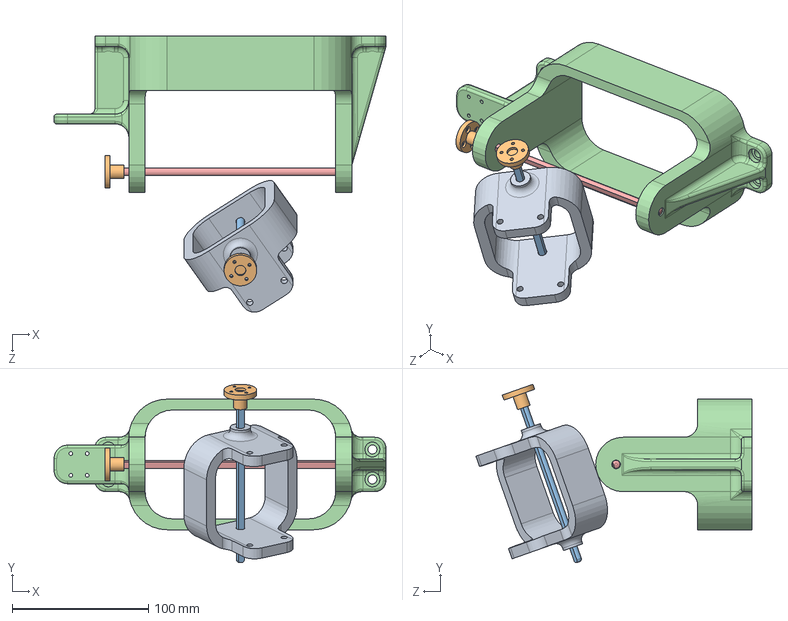
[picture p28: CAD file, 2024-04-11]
Mécanique/3D CAD/En cours/Épaule_test_2/Épaule.SLDASM
244.0 x 131.2 x 203.0 mm
Adaptateur x 2
Shaft_long_court
Shaft_long

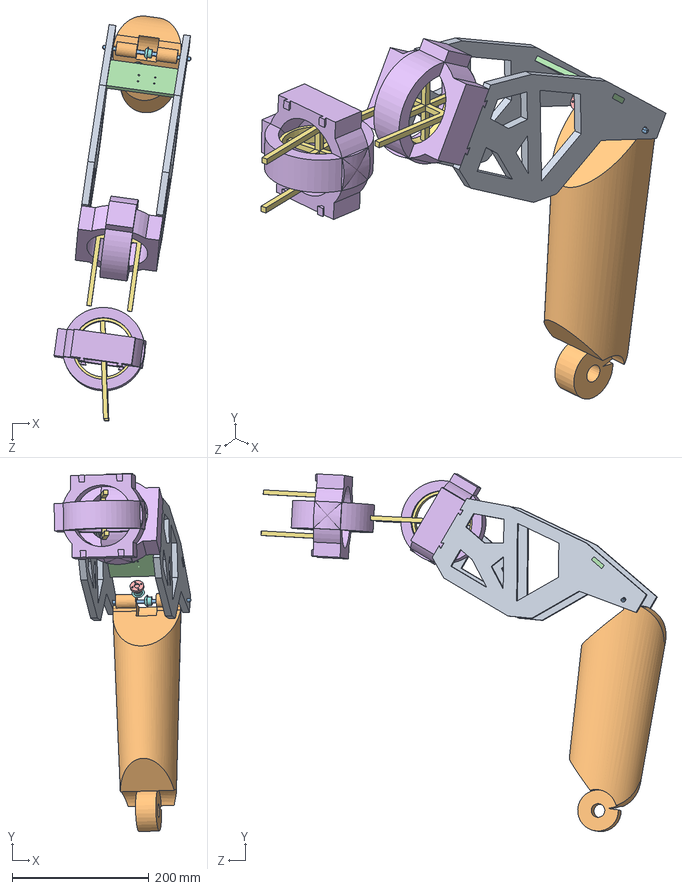
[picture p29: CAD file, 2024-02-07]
Mécanique/3D CAD/V4_Robot_Arm/Arm.SLDASM
199.9 x 523.1 x 591.5 mm
bicep_1
Épaule_2.1 x 2
Épaule_2.2 x 2
Engrenage_coude x 2

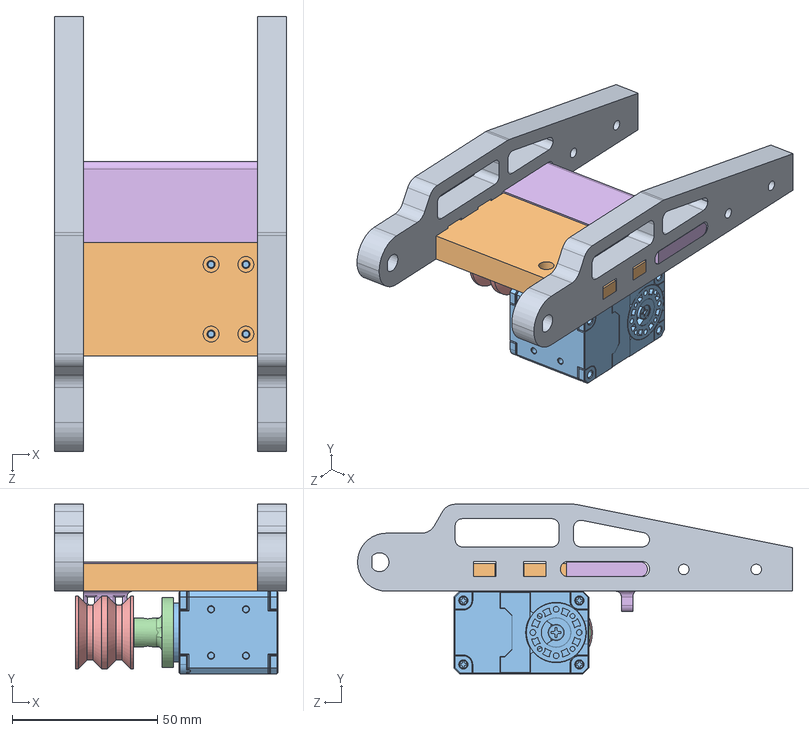
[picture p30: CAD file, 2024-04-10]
Mécanique/3D CAD/En cours/Avant_Bras/Avant_bras_complet.SLDASM
80.0 x 58.5 x 150.0 mm
Avant_Bras x 2
Support_Avant_Bras_Moteur
Petit_moteur
Poulie
Poulie_2
Support_files_main

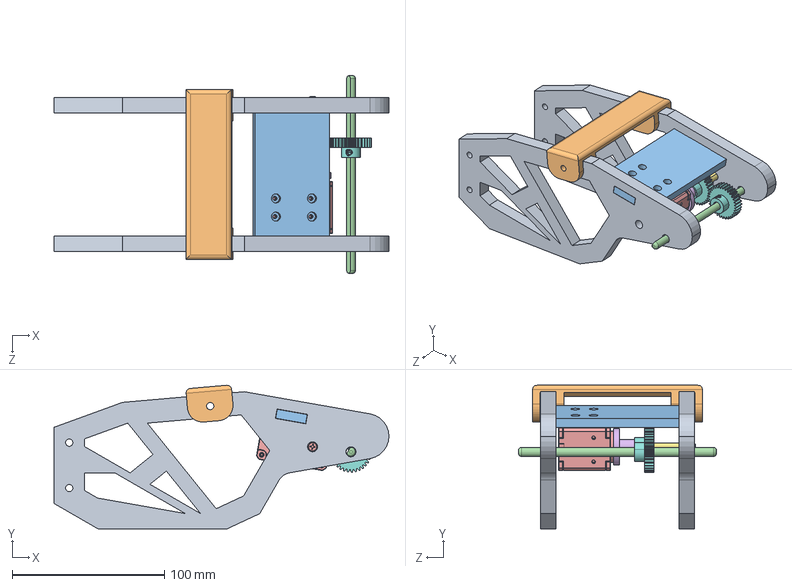
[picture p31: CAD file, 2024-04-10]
Mécanique/3D CAD/En cours/Coude_VF/Coude_VF.SLDASM
220.0 x 94.3 x 130.0 mm
Bicep_base x 2
Fixation_bicep
Fixation_moteur
Shaft_long_court
Petit_moteur
Adaptateur
Shaft
Gear_32T x 2

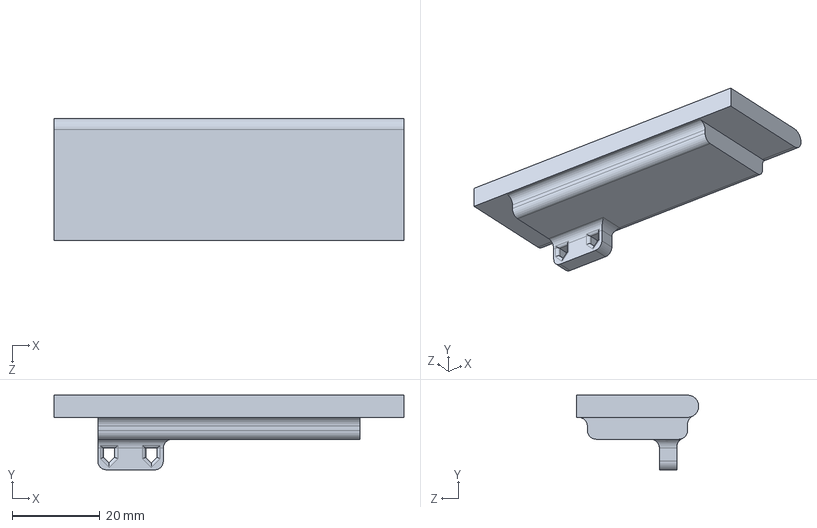
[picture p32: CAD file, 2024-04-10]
Mécanique/3D CAD/En cours/Avant_Bras/Support_files_main.SLDPRT
80.0 x 17.1 x 28.0 mm

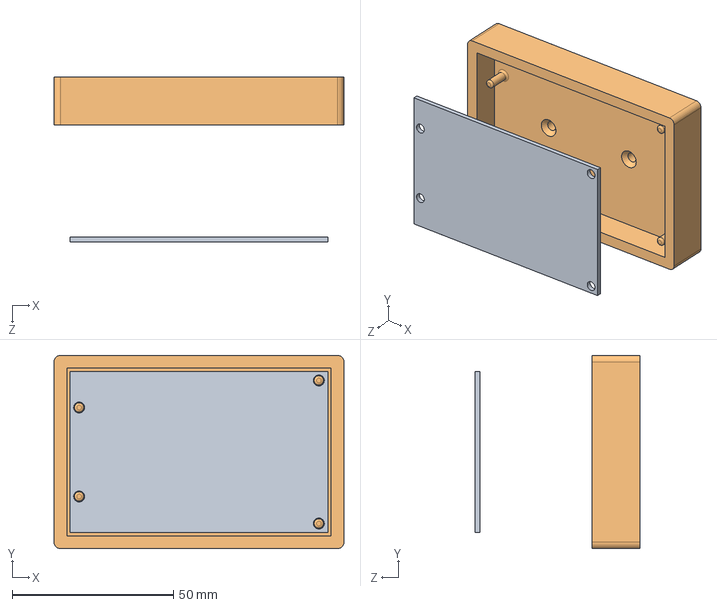
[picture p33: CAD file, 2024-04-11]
Mécanique/3D CAD/En cours/Support_openRB/Assembly.SLDASM
90.0 x 60.0 x 51.3 mm
Arduino
Support

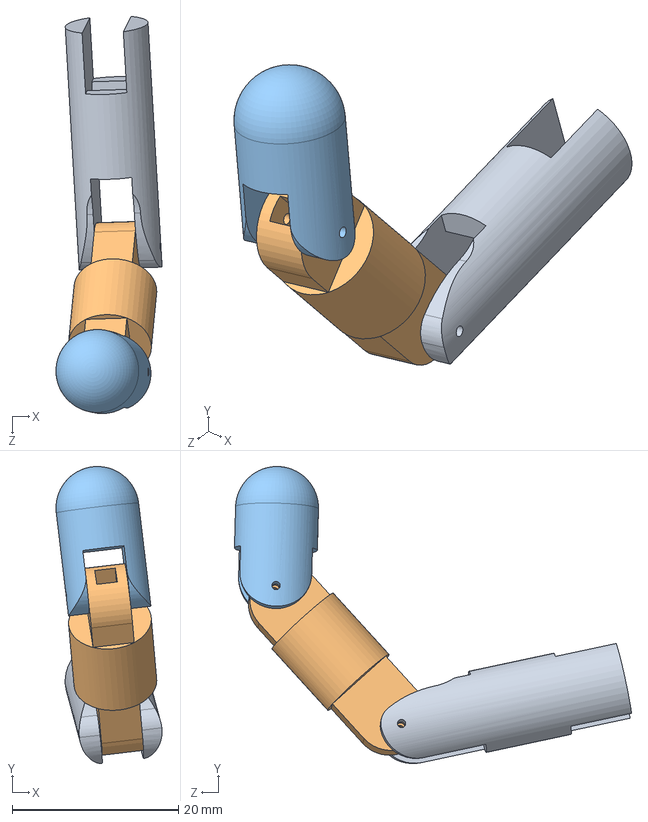
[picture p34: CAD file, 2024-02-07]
Mécanique/3D CAD/En cours/doigt/Assem2.SLDASM
12.8 x 35.8 x 47.8 mm
Doigt_1
Doigt_2.1
Doigt_3

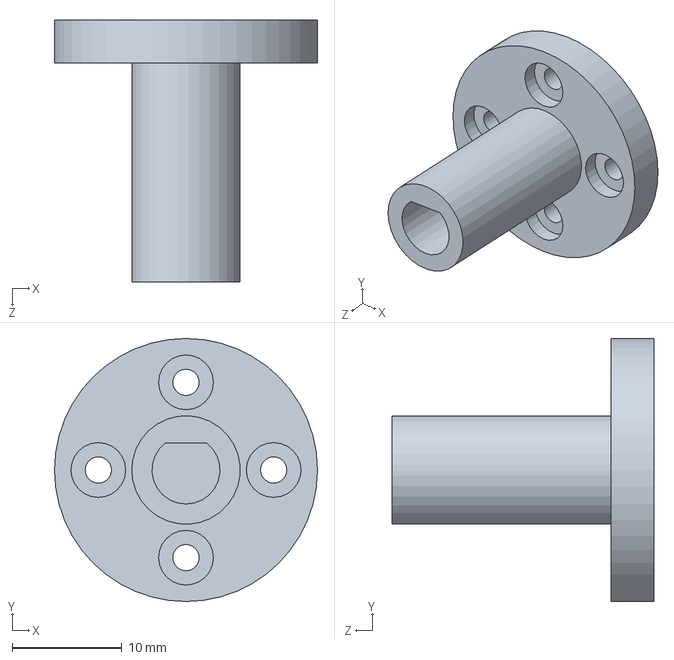
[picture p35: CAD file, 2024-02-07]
Mécanique/3D CAD/Adaptateur moteur/Adaptateur_621.SLDPRT
24.0 x 24.0 x 23.9 mm

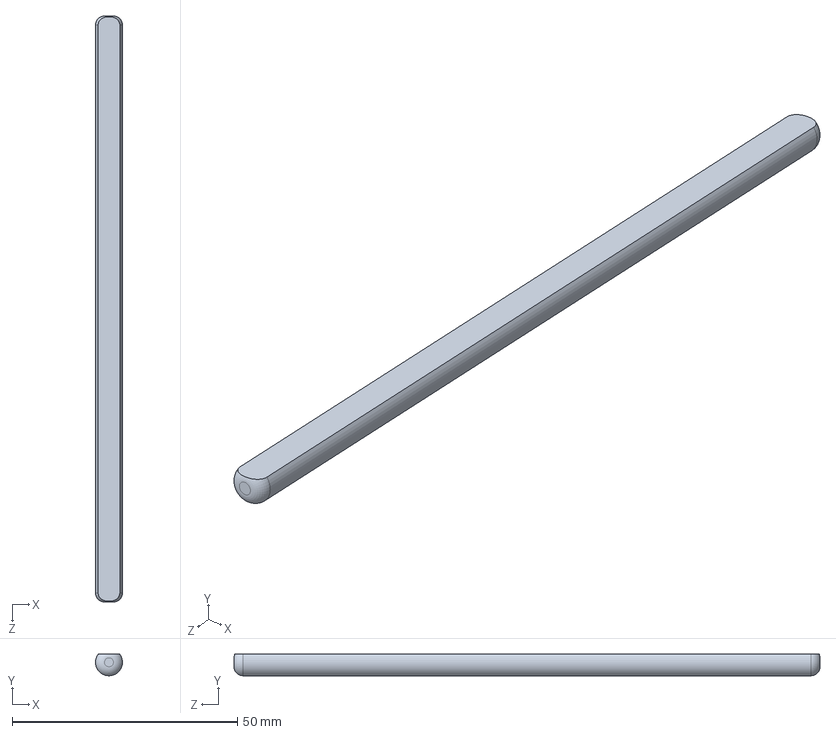
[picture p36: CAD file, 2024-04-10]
Mécanique/3D CAD/En cours/Coude_VF/Shaft_long_court.SLDPRT
5.99 x 4.80 x 130.0 mm

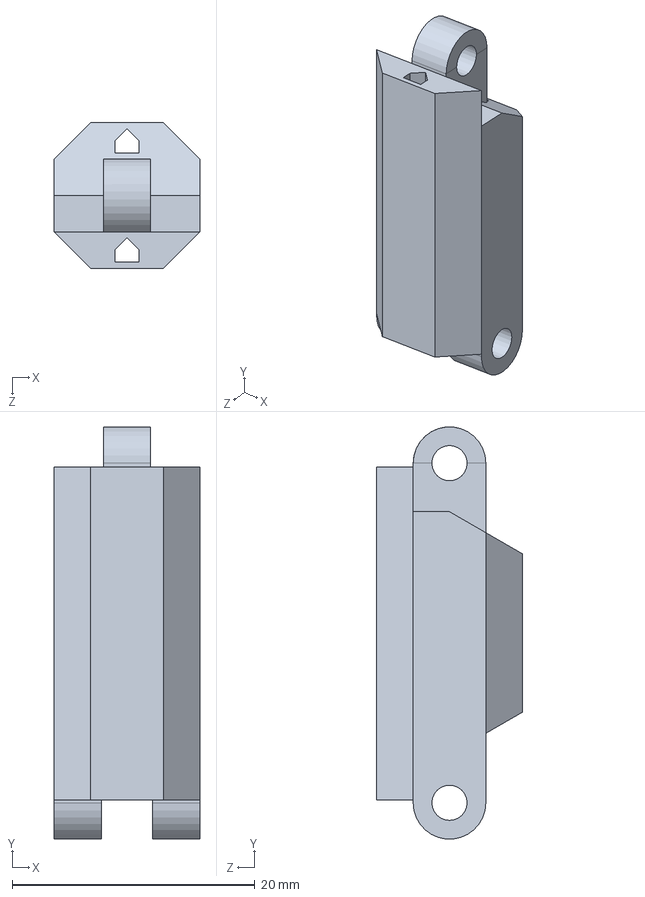
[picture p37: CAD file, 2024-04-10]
Mécanique/3D CAD/En cours/doigt/Doigt_test_1.SLDPRT
12.0 x 34.0 x 12.0 mm

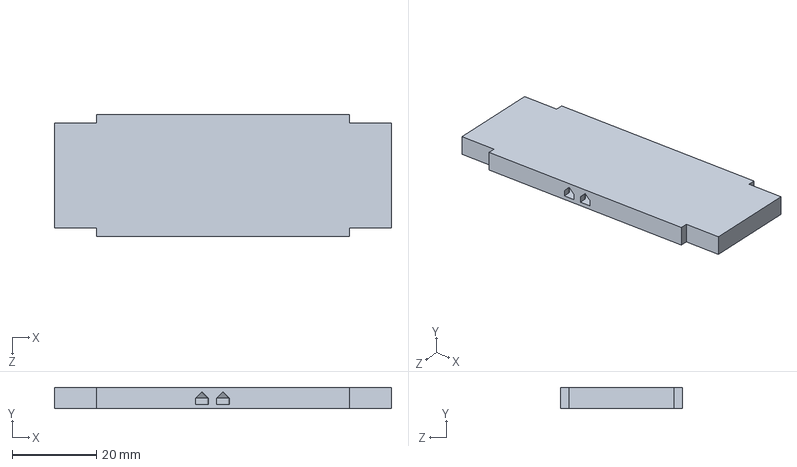
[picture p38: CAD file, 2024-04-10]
Mécanique/3D CAD/En cours/Support/Support_orientation_fil.SLDPRT
80.0 x 5.00 x 29.0 mm

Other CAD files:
Mécanique/3D CAD/En cours/Support_openRB/arduino-mkr-connector-carrier.SLDASM
Mécanique/3D CAD/En cours/Support_openRB/Arduino.SLDPRT
Mécanique/3D CAD/Impression/Bicep_x2.STL
Mécanique/3D CAD/Impression/Impression Gino/Support_Avant_Bras_Moteur.STL
Mécanique/3D CAD/Adaptateur moteur/Adaptateur_601.SLDPRT
Mécanique/3D CAD/Adaptateur moteur/Adaptateur_611.SLDPRT
Mécanique/3D CAD/Adaptateur moteur/Adaptateur_631.SLDPRT
Mécanique/3D CAD/Adaptateur moteur/Adaptateur_641.SLDPRT
Mécanique/3D CAD/Adaptateur moteur/Adaptateur_651.SLDPRT
Mécanique/3D CAD/Adaptateur moteur/Adaptateur_661.SLDPRT
Mécanique/3D CAD/Adaptateur moteur/Adaptateur_Good.SLDPRT
Mécanique/3D CAD/Coude/001_Coude.SLDPRT
Mécanique/3D CAD/Coude/003_Coude.SLDPRT
Mécanique/3D CAD/Coude/004_Coude.SLDPRT
Mécanique/3D CAD/Coude/Coude_V1.SLDASM
Mécanique/3D CAD/Coude/Engrenage_Coude.SLDPRT
Mécanique/3D CAD/Coude/Fixation.SLDPRT
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

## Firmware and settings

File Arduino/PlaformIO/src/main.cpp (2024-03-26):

/*******************************************************************************
* Copyright 2016 ROBOTIS CO., LTD.
*
* Licensed under the Apache License, Version 2.0 (the "License");
* you may not use this file except in compliance with the License.
* You may obtain a copy of the License at
*
*     http://www.apache.org/licenses/LICENSE-2.0
*
* Unless required by applicable law or agreed to in writing, software
* distributed under the License is distributed on an "AS IS" BASIS,
* WITHOUT WARRANTIES OR CONDITIONS OF ANY KIND, either express or implied.
* See the License for the specific language governing permissions and
* limitations under the License.
*******************************************************************************/


#include <Arduino.h>
#include <Dynamixel2Arduino.h>
#include "serialCommunication.h"

//OpenRB does not require the DIR control pin.
#define DXL_SERIAL Serial1
#define DEBUG_SERIAL Serial
const int DXL_DIR_PIN = -1;

const float DXL_PROTOCOL_VERSION = 2.0;
Dynamixel2Arduino dxl(DXL_SERIAL, DXL_DIR_PIN);

//This namespace is required to use Control table item names
using namespace ControlTableItem;

// put function declarations here:
void set_speed(uint8_t id, float speedPct);
void homing();
//void printPosition();
//int choiceMovement(int command);
void check_pos_achieved(float *target, int i);
void setGoal_Position(float *target, int pos);
//void setGoalSpeed(float *target, int pos);
void limitPosition(float *target_angle);
float getSpeed(int motor, float target);
void setAngularSpeed(float *target);
void setAngularPosition(float *target);
void changeAngle(float* target);


// ========== Variables à modifier selon le contexte d'utilisation ========== // 
const int nb_motor = 3;
const int nb_movement = 3;
const uint8_t DXL_ID[nb_motor] = {1, 20, 3}; //Motor ID
float min_pos_motor[nb_motor] = {115, 2, 0};
float max_pos_motor[nb_motor] = {278, 143, 227};
float upper_speed_limit = 0.9;
float lower_speed_limit = 0.1;
float msg_data[nb_motor] = {0,0,0};

int nb_target = 12;
struct structStance{ 
  int stance_id;
  int nb_sub_movement;
  float target[12]; // motor position (in degree)
};

struct structStance stancePosition[nb_movement] = {
  // Home
  {0, 1 ,{190.0, 140.0, 65.0,
          200.0, 170.0, 150.0,
          200.0, 170.0, 150.0,
          200.0, 170.0, 150.0}},

  // Curl
  {1, 1, {150.0, 170.0, 280.0, 
          150.0, 170.0, 280.0, 
          150.0, 170.0, 280.0, 
          150.0, 170.0, 280.0}},

  // Jab
  {2, 3, {196.0, 85.0, 305.0, 
          110.4, 85.0, 178.5, 
          196.0, 85.0, 305.0,
          196.0, 85.0, 305.0}},
};

struct structStance stanceSpeed[nb_movement] = {
  // Home
  {0, 1 ,{0.3, 0.3, 0.3,
          0.3, 0.3, 0.3,
          0.3, 0.3, 0.3, 
          0.3, 0.3, 0.3}},
  
  // Curl
  {1, 1, {0.2, 0.3, 0.2,
          0.3, 0.3, 0.3,
          0.3, 0.3, 0.3, 
          0.3, 0.3, 0.3}},

  // Jab
  {2, 3, {0.35, 0.35, 0.6, 
          0.35, 0.35, 0.6,
          0.35, 0.35, 0.6,
          0.35, 0.35, 0.6,}},
};


void setup() {
  // Use UART port of DYNAMIXEL Shield to debug.
  DEBUG_SERIAL.begin(115200);
  while(!DEBUG_SERIAL);

  // Set Port baudrate to 57600bps. This has to match with DYNAMIXEL baudrate.
  dxl.begin(57600);
  // Set Port Protocol Version. This has to match with DYNAMIXEL protocol version.
  dxl.setPortProtocolVersion(DXL_PROTOCOL_VERSION);
  
  // initialise each motor
  for (int i=0;i<nb_motor;i++){
    dxl.ping(DXL_ID[i]);
    dxl.torqueOff(DXL_ID[i]);
    dxl.setOperatingMode(DXL_ID[i], OP_POSITION);
    dxl.torqueOn(DXL_ID[i]);
    set_speed(DXL_ID[i],0.2);
  }
  
   homing();

}



// fonction loop() pour les mouvements préenregistés
/*
void loop() {
  while (!Serial.available()) {
    int chosen_command = 0;
    chosen_command = Serial.readString().toInt();
    //Serial.print(chosen_command);
    
    if (chosen_command <= 0){
      chosen_command = 0;
    }

    if (chosen_command < nb_movement){
      for (int i=0; i<stancePosition[chosen_command].nb_sub_movement*nb_motor; i+=nb_motor){
        //setGoalSpeed(stanceSpeed[chosen_command].target,i);
        setGoal_Position(stancePosition[chosen_command].target,i);
        check_pos_achieved(stancePosition[chosen_command].target,i);
      }
      homing();
    }
  }
}*/


// fonction loop() pour le temps réel
void loop(){
  bool data_received = getSerialMessage(msg_data);
  if (data_received){
    limitPosition(msg_data);
    setAngularSpeed(msg_data);
    setAngularPosition(msg_data);
  }
}



void homing(){
  setGoal_Position(stancePosition[0].target,0);
  check_pos_achieved(stancePosition[0].target, 0);
}



// ==================== Fonction pour temps réel =================== // 
void changeAngle(float* target){
  target[0] = 360 - target[0];
  target[2] = 90 - target[2];
  target[0] = map(target[0],270,360,min_pos_motor[0], 190);
  target[2] = map(target[2],0,180,min_pos_motor[2], max_pos_motor[2]);
}

void limitPosition(float *target_angle){
  for(int i=0;i<nb_motor;i++){
    if (target_angle[i] < min_pos_motor[i]){
      target_angle[i] = min_pos_motor[i];
    }
    if (target_angle[i] > max_pos_motor[i]){
      target_angle[i] = max_pos_motor[i];
    }
  }
}

void setAngularSpeed(float *target){
  float erreur_pos[nb_motor] = {0,0,0};
  float max_erreur = 0;
  for(int i=0;i<nb_motor;i++){
    float present_pos = dxl.getPresentPosition(DXL_ID[i], UNIT_DEGREE);
    erreur_pos[i] = abs(target[i] - present_pos);
    if (erreur_pos[i] > max_erreur) {
      max_erreur = erreur_pos[i];
    }
  }
  float gain = 0.9/max_erreur;
  for(int i=0;i<nb_motor;i++){
    float speed_pct = erreur_pos[i]*gain;
    set_speed(DXL_ID[i], speed_pct);
  }
}

void setAngularPosition(float *target){
  for (int i=0;i<nb_motor;i++){
    dxl.setGoalPosition(DXL_ID[i], target[i], UNIT_DEGREE);
  }
}



// ==================== Fonction pour mouvements préenregistrés =================== // 
void setGoal_Position(float *target, int pos){
  int motor=0;
  for(int i=pos;i<pos+nb_motor;i++){
    float speed_pct = getSpeed(motor, target[i]);
    set_speed(DXL_ID[motor], speed_pct);
    dxl.setGoalPosition(DXL_ID[motor], target[i], UNIT_DEGREE);
    motor++;
  }
}

float getSpeed(int motor, float target){
  // Égal à 1/220. Donc, pour une erreur d'angle de 220 deg, la vitesse est 100% (les moteurs ne tourneront pas plus de 270 deg) 
  float p_gain = 0.004545455;
  float error = abs(dxl.getPresentPosition(DXL_ID[motor], UNIT_DEGREE) - target);
  float out_speed = error*p_gain;
  return out_speed; 
}

void check_pos_achieved(float *target, int j){
  bool ready = false;
  float interval = 5.0;
  while (ready == false){
    int total = 0;
    int target_index = j;
    for (int i=0;i<nb_motor;i++){
      float pos_motor = dxl.getPresentPosition(DXL_ID[i], UNIT_DEGREE);
      if (abs(target[target_index]-pos_motor)<interval){
        total += 1;
      }
      target_index += 1;
    }
    if (total == nb_motor){
      ready = true;
    }
    else if (total > nb_motor){
      Serial.println("Le check pour savoir si les moteurs sont arrives a destination n'est pas bien fait");
    }
  }
}

void set_speed(uint8_t id, float speedPct) {
  if (speedPct > upper_speed_limit){
    speedPct = upper_speed_limit;
  }
  if (speedPct < lower_speed_limit){
    speedPct = lower_speed_limit;
  }
  double maxDynamixelSpeed = 234.267; // Speed (RPM) = 1023*0.229 [valeurs provenant des fiches techniques des Dynamixels]
  uint32_t newSpeedRpm = speedPct*maxDynamixelSpeed;
  uint32_t writeTimeout = 100; //ms
  dxl.writeControlTableItem(PROFILE_VELOCITY, id, newSpeedRpm, writeTimeout);
}




// ==================== Anciennes fonctions =================== // 
/*
void printPosition(){
  for(int i=0;i<nb_motor;i++){
    float present_position = dxl.getPresentPosition(DXL_ID[i], UNIT_DEGREE);
    DEBUG_SERIAL.print("Present_Position ");
    DEBUG_SERIAL.print(i);
    DEBUG_SERIAL.print(" (degree) : ");
    DEBUG_SERIAL.println(present_position);
  }
}*/

/*
int choiceMovement(int command){
  for (int i=0;i<nb_movement;i++){
    if (command == stancePosition[i].stance_id){
      return i;
    } 
  }
  return -1;
}*/

/*
void setGoalSpeed(float *target, int pos){
  int motor=0;
  for(int i=pos;i<pos+nb_motor;i++){
    set_speed(DXL_ID[motor], target[i]);
    motor++;
  }
}*/

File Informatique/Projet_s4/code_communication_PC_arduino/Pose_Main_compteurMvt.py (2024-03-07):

#import time

import mediapipe as mp
import numpy as np
import cv2
import serial
import time

mp_drawing = mp.solutions.drawing_utils
mp_pose = mp.solutions.pose
mp_hand = mp.solutions.hands
#arduino = serial.Serial(port='COM5',   baudrate=115200, timeout=.1)

# VIDEO FEED
cap = cv2.VideoCapture(0)
#initiate holistic model

# curl counter
counter = 0
stage = None

# shoulder counter
counterB = 0
stageB = None

#shoulder counter
counterC = 0
stageC = None

#shoulder counter
counterD = 0
stageD = None

with (mp_hand.Hands(min_detection_confidence=0.5, min_tracking_confidence=0.5) as hands):
    with (mp_pose.Pose(min_detection_confidence=0.5, min_tracking_confidence=0.5) as pose):
        while cap.isOpened():
            ret, frame = cap.read()
            #recolor image to rgb
            image = cv2.cvtColor(frame, cv2.COLOR_BGR2RGB)
            image.flags.writeable = False
            #make detection
            results = pose.process(image)
            results_hand = hands.process(image)
            #recolor back to RGB
            image.flags.writeable = True
            image = cv2.cvtColor(image, cv2.COLOR_RGB2BGR)

            def calculate_angle(a, b, c):
                a = np.array(a)
                b = np.array(b)
                c = np.array(c)

                radians = np.arctan2(c[1]-b[1], c[0]-b[0]) - np.arctan2(a[1]-b[1], a[0]-b[0])
                angle = np.abs(radians*180.0/np.pi)

                if angle >180.0:
                    angle = 360-angle

                return angle

            """def write_read(x):
                arduino.write(bytes(x,   'utf-8'))
                time.sleep(0.05)
                data = arduino.readline()
                return   data"""

            #Extract Landmarks
            try:
                landmarks = results.pose_landmarks.landmark

                shoulder = [landmarks[mp_pose.PoseLandmark.LEFT_SHOULDER.value].x,
                            landmarks[mp_pose.PoseLandmark.LEFT_SHOULDER.value].y]

                elbow = [landmarks[mp_pose.PoseLandmark.LEFT_ELBOW.value].x,
                         landmarks[mp_pose.PoseLandmark.LEFT_ELBOW.value].y]

                wrist = [landmarks[mp_pose.PoseLandmark.LEFT_WRIST.value].x,
                         landmarks[mp_pose.PoseLandmark.LEFT_WRIST.value].y]

                hip = [landmarks[mp_pose.PoseLandmark.LEFT_HIP.value].x,
                         landmarks[mp_pose.PoseLandmark.LEFT_HIP.value].y]

                shoulderB = [landmarks[mp_pose.PoseLandmark.LEFT_SHOULDER.value].y,
                            landmarks[mp_pose.PoseLandmark.LEFT_SHOULDER.value].z]

                elbowB = [landmarks[mp_pose.PoseLandmark.LEFT_ELBOW.value].y,
                         landmarks[mp_pose.PoseLandmark.LEFT_ELBOW.value].z]

                wristB = [landmarks[mp_pose.PoseLandmark.LEFT_WRIST.value].y,
                         landmarks[mp_pose.PoseLandmark.LEFT_WRIST.value].z]

                hipB = [landmarks[mp_pose.PoseLandmark.LEFT_HIP.value].y,
                         landmarks[mp_pose.PoseLandmark.LEFT_HIP.value].z]

                shoulderC = [landmarks[mp_pose.PoseLandmark.RIGHT_SHOULDER.value].x,
                            landmarks[mp_pose.PoseLandmark.RIGHT_SHOULDER.value].y]

                angle = calculate_angle(shoulder, elbow, wrist)
                angleB = calculate_angle(hip, shoulder, elbow)
                angleC = calculate_angle(hipB, shoulderB, elbowB)
                angleD = calculate_angle(shoulderC, shoulder, elbow)

                cv2.putText(image, str(angle),
                            tuple(np.multiply(elbow,[640, 480]).astype(int)),
                                  cv2.FONT_HERSHEY_SIMPLEX, 0.5, (255, 255, 255), 2, cv2.LINE_AA, )

                """cv2.putText(image, str(angleB),
                            tuple(np.multiply(shoulder, [640, 480]).astype(int)),
                                  cv2.FONT_HERSHEY_SIMPLEX, 0.5, (255, 255, 255), 2, cv2.LINE_AA, )"""
                cv2.putText(image, str(angleC),
                            tuple(np.multiply(shoulder, [640, 480]).astype(int)),
                            cv2.FONT_HERSHEY_SIMPLEX, 0.5, (255, 255, 255), 2, cv2.LINE_AA, )

                ret = "rien"
                # curl counter logic
                if angle > 160 and angleB < 10:
                    stage = "down"
                if angle < 30 and stage == "down" and angleB < 20:
                    stage = "up"
                    counter += 1
                    #ret = write_read("1")



                #Shoulder counter logic
                if angleC < 50:
                    stageC = "down"
                if 80 < angleC < 100 and stageC == "down" and angleD < 170 and stageD != "up":
                    stageC = "up"
                    counterC += 1
                    #ret = write_read("3")


                # shoulder counter logic
                if angleB > 150:
                    stageB = "down"
                if angleB < 30 and stageB == "down" and angleC < 150 and stageC != "up":
                    stageB = "up"
                    counterB += 1
                    #ret = write_read("2")

                #Shoulder counter logic
                if angleD < 110:
                    stageD = "down"
                if angleD > 170 and stageD == "down" and stageC != "up":
                    stageD = "up"
                    counterD += 1
                    #ret = write_read(4)
                if ret != "rien":
                    print(ret)






            except:
                pass

            cv2.rectangle(image, (0, 0), (112, 72), (245, 117, 16), -1)

            cv2.putText(image,'REPS', (15, 12),
                        cv2.FONT_HERSHEY_SIMPLEX, 0.5, (0, 0, 0), 1,cv2.LINE_AA)

            cv2.putText(image, str(counter), (10, 60),
                        cv2.FONT_HERSHEY_SIMPLEX, 2, (255, 255, 255), 2,cv2.LINE_AA)

            """cv2.putText(image,'STAGE', (65, 12),
                        cv2.FONT_HERSHEY_SIMPLEX, 0.5, (0, 0, 0), 1,cv2.LINE_AA)
    
            cv2.putText(image, stage, (60, 60),
                        cv2.FONT_HERSHEY_SIMPLEX, 2, (255, 255, 255), 2,cv2.LINE_AA)"""

            cv2.rectangle(image, (112, 0), (224, 72), (30, 240, 16), -1)

            cv2.putText(image,'REPS', (120, 12),
                        cv2.FONT_HERSHEY_SIMPLEX, 0.5, (0, 0, 0), 1,cv2.LINE_AA)

            cv2.putText(image, str(counterB), (120, 60),
                        cv2.FONT_HERSHEY_SIMPLEX, 2, (255, 255, 255), 2,cv2.LINE_AA)

            """cv2.putText(image,'STAGE', (310, 12),
                        cv2.FONT_HERSHEY_SIMPLEX, 0.5, (0, 0, 0), 1,cv2.LINE_AA)
    
            cv2.putText(image, stageB, (290, 60),
                        cv2.FONT_HERSHEY_SIMPLEX, 2, (255, 255, 255), 2,cv2.LINE_AA)"""


            cv2.rectangle(image, (224, 0), (336, 72), (30, 16, 240), -1)
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

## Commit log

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2024-01-23 Ajout homing
    Ajout de ka fonction de homing et définition de variables globales
2024-01-29 Quasi prêt pour le curl
    Code presque prêt pour faire un curl.
    Manque la communication entre le système de vision et l'arduino.
    Le code n'est pas assez modulaire pour ajouter d'autre mouvements
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2024-02-07 Ajout de toute les versions précédente, bcp de fichier ne sont plus bon
    [0001.SLDPRT, 0002.SLDPRT, 001.SLDPRT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]
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2024-02-07 Ajout fichier Gino
    [Avant_Bras.SLDPRT, Avant_Bras_20cm.STL, Avant_Bras_old.SLDPRT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]
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2024-02-07 V1_épaule en test
    [0001.SLDPRT, Adaptateur.SLDPRT, Shaft.SLDPRT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]
2024-02-07 Assemblage Avant-bras
    [Avant_bras_complet.SLDASM]
2024-02-07 Épaule sans le rouge
    [0001.SLDPRT, Shaft.SLDPRT]
2024-02-07 Assemblage Main
    [Avant_bras_complet.SLDASM, Main.SLDASM, Support.SLDPRT]
2024-02-07 2e join épaule modifié
    [0002.SLDPRT]
2024-02-07 Bicep 81 mm
    [Bicep_base.SLDPRT, Coude_VF.SLDASM, Fixation_bicep.SLDPRT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]
2024-02-07 Assemblage main correction
    [Main.SLDASM]
2024-02-07 Épaule_V2
    [0001.SLDPRT, 0002.SLDPRT, Épaule.SLDASM]
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2024-02-07 Modification d'épaule pour print + bras complet
    [0001.SLDPRT, 0002.SLDPRT, Assemblage1.SLDASM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]
2024-02-13 Pin carré amincie pour meilleur fit
    [Support_Carre_Court.SLDPRT, Support_Carre_Court.STL, Épaule.SLDASM]
2024-02-13 Support complet modifier avec un jeu
    [0001.SLDPRT, 0002.SLDPRT, Support_Avant_Bras.SLDPRT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]
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2024-02-14 Modification suite a quelque commentaire au studio. Assemblage modifier, rendu à ajouter engrenage au coude et adapter les trous pour le moteur en fonction des engrenage choisi
    [Assemblage1.SLDASM, Avant_bras_complet.SLDASM, Coude_VF.SLDASM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]
2024-02-14 Fichier modifier
    [0001.SLDPRT, 0002.SLDPRT, 001.SLDPRT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]
2024-02-14 Dossier replacé
    [Adaptateur_601.STL, Adaptateur_611.STL, Adaptateur_621.STL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]
2024-02-14 Communication Python-Arduino corrigée
2024-02-14 Avant-bras modif
    [Avant_Bras.SLDPRT, Support_Avant_Bras_Moteur.SLDPRT]
2024-02-14 Bicep modif
    [0002.SLDPRT, 0002.STL, Adaptateur.SLDPRT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]
2024-02-14 Modif paume 1
    [Paume_V3.SLDPRT]
2024-02-14 Modifications épaule + début base
    [0001.SLDPRT, 0001.STL, 0002.SLDPRT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]
2024-02-18 Modifications Final épaule V3
    [0001.SLDPRT, 0001.STL, 0003.SLDPRT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]
2024-02-19 fin de semaine
    [Assem2.SLDASM, Doigt1.SLDPRT, Doigt2.SLDPRT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]
2024-02-21 Doigt v4
    [Doigt1.SLDPRT, Doigt1.STL, Doigt2.SLDPRT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]
2024-02-21 Modification de l'emplacement du moteur coude
    [Adaptateur.SLDPRT, Bicep_base.SLDPRT]
2024-02-21 Modif emplacement moteur coude
    [Coude_VF.SLDASM, Fixation_moteur.SLDPRT]
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2024-02-21 design main
    [Assem1.SLDASM, Assemblage1.SLDASM, Avant_bras_complet.SLDASM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]
2024-02-21 Nouveau repère pour bon centre de masse avant bras
    [Avant_bras_complet.SLDASM]
2024-02-21 Épaule V3
    [0001.SLDPRT, 0001.STL, 0002.SLDPRT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]
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2024-02-21 Paume troue v1
    [Paume_V3.SLDPRT]
2024-02-22 Meilleur troue
    [Paume_V3.SLDPRT]
2024-02-22 Paume avec troue
    [Paume_V3.SLDPRT]
2024-02-22 Paume STL
    [Paume_V3.STL]
2024-02-25 Config PlatformIO
    [arduino_zero.cfg]
2024-02-27 Modification du centre de coordonnées de l'avant Bras
    [Avant_bras_complet.SLDASM]
2024-02-27 test assemblage main
    [Doigt1.SLDPRT]
2024-02-27 Bonne main
    [Main.SLDASM]
2024-02-27 Ajustement dans SW et dans MG
    Syst de coordonnées sur SW pour Av et M
    Inertie, Avcm, Mcm ajusté dans MG
    [Avant_bras_complet.SLDASM, Main.SLDASM]
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2024-03-12 Correction d'erreur
    Correction d'erreurs dans le code de communication par port série. Il faut changer getSerial() pour modifier un array et en retourner un
    [main.cpp, serialCommunication.cpp]
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2024-03-13 Modif ReadMe Mec et limite de déplacement de l'assemblage
    [Assemblage1.SLDASM, Avant_bras_complet.SLDASM, Coude_VF.SLDASM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]
2024-03-13 moins de jeux pour doigt
    [Assemb_test.SLDASM, Doigt_test_1.SLDPRT, Doigt_test_2.SLDPRT]
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2024-03-20 doigt good
    [Doigt1.STL, Doigt2.STL, Doigt_3.STL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]
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2024-03-20 beau trou (ta mère)
    [Paume_V3.SLDPRT, Paume_V3.STL, Paume_V4.SLDPRT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]
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2024-03-20 1:1 coude
    [Bicep_base.SLDPRT]
2024-03-20 Impressioon new_bicep
    [Bicep_base - Adaptateur-1.STL, Bicep_base - Bicep_base-1.STL, Bicep_base - Bicep_base-2.STL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]
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2024-03-27 New poulie
    [Bicep_base.SLDPRT, Poulie.SLDPRT, Poulie_1.STL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]
2024-03-27 Paume corriger/dossier cleaner
    [Assem1.SLDASM, Assemb_test.SLDASM, Bon_doigt_1.STL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]
2024-03-27 Print_poulie et biceps
    [Poulie.SLDASM]
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2024-04-03 Modification assemblage
    Assemblage main, finalisation de l'avant bras avec nouveau support file pour la main
    [Assemblage1.SLDASM, Avant_bras_complet.SLDASM, Coude_VF.SLDASM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]
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2024-04-06 support moteur
    [Support_Avant_Bras_Moteur.SLDPRT]
2024-04-07 Passage de fil
    [Avant_Bras_PassageFil.SLDPRT]
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2024-04-10 Support de l'orientation des fils
    [Support_orientation_fil.SLDPRT, Support_orientation_fil.STL]
2024-04-10 figure 4
    [Doigt_test_1.SLDPRT, main.SLDASM]
2024-04-10 Support Moteur STL et Allignement
    [Assemblage1.SLDASM, Avant_bras_complet.SLDASM, Coude_VF.SLDASM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]
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2024-04-11 Readme Mec
    [Poulie.SLDASM, Poulie_1.SLDPRT]
2024-04-11 Ca marche full bien
    [Épaule.SLDASM]
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2024-04-14 Changement structure du Git
    [arduino_zero.cfg]
